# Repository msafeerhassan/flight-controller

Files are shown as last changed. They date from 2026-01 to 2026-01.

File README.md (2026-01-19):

# Custom Flight Controller
## A completely custom high-efficiency Flight Controller for Drone.
This flight controller is based on STM32F722RET6 MCU and BMI270 Gyro. This is optimized for modern FPV Drones featuring a 4 layer PCB and a dedicated 8-Pin connecter for modern ESC's.

### Hardware Specifications

MCU: STM32F722RET6

Gyro: BMI270 via Serial Peripheral Interface

Storage: W25NO1G

Input Voltage: 3S-6S LiPo (integrated 5V/2A Regulator)

OSD: AT7456E

Features: Buzzer for emergency situation, USB-C Programming, Suitable capacitors, diodes, inductors and resistors

### ESC Connection Guide
Pin 1 : VBAT : Battery Input

Pin 2 : GND : Ground

Pin 3 : Motor 1 : PB4

Pin 4 : Motor 2 : PB5

Pin 5 : Motor 3 : PB0

Pin 6 : Motor 4 : PB1

Pin 7 : Current : PC0

Pin 8 : Telemetry : PC7

### Software Specifications
Compatible with: 
- Betaflight
- Rotorflight
##### Code is given in firmware folder

### PCB:



### Schematic Diagram:



### Designed by Safeer Hassan :)

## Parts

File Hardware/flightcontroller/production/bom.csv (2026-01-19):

Designator | Footprint | Quantity | Value | LCSC Part #
BZ1 | Buzzer_12x9.5RM7.6 | 1 | Buzzer
C1, C12, C15, C16, C17, C18, C2, C3, C4, C6 | 0603 | 10 | 100nF
C10, C13, C8, R11, R12 | 0805 | 5 | 22uF
C11, C5, C9 | 0805 | 3 | 10uF
C14 | 0603 | 1 | 1uF
C19 | 0805 | 1 | 4.7uF
C7 | 0603 | 1 | 2.2uF
D1 | D_SOD-123 | 1 | B5819W_C8598
D2 | 0603 | 1 | GREEN LED
D3 | 0603 | 1 | RED LED
D4, D5 | D_SOD-123 | 2 | D_Schottky
D6 | D_DO-35_SOD27_P7.62mm_Horizontal | 1 | 1N4148
J1 | USB_C_Receptacle_HRO_TYPE-C-31-M-12 | 1 | USB_C_Receptacle_USB2.0
J3 | JST_GH_BM04B-GHS-TBT_1x04-1MP_P1.25mm_Vertical | 1 | A
J5 | Tag-Connect_TC2030-IDC-NL_2x03_P1.27mm_Vertical | 1 | JTAG_TC2030
L1 | L_6.3x6.3_H3 | 1 | CSME0418D-4R7M-LRH
P1 | JST_SHL_SM08B-SHLS-TF_1x08-1MP_P1.00mm_Horizontal | 1 | SM08B-SRSS-TB(LF)(SN) | C160407
Q1 | SOT-23 | 1 | MMBT2222A
R1, R2, R3, R4, R7, R8 | 0603 | 6 | 10k
R10, R9 | 1210 | 2 | 47uF
R13 | 0603 | 1 | 1k
R5, R6 | 0603 | 2 | 5.1k
SW1 | SW_Push_SPST_NO_Alps_SKRK | 1 | SW_Push
U2 | TSOT-23-6 | 1 | AP63205WU
U4 | SOT-23-6 | 1 | USBLC6-2SC6
U5 | SOT-23-5 | 1 | XC6220B331MR
U6 | LQFP-64_10x10mm_P0.5mm | 1 | STM32F722RETx
U7 | LGA-14_3x2.5mm_P0.5mm_LayoutBorder3x4y | 1 | BMI270
U8 | Bosch_LGA-8_2x2.5mm_P0.65mm_ClockwisePinNumbering | 1 | SPL06-001
U9 | WSON-8-1EP_8x6mm_P1.27mm_EP3.4x4.3mm | 1 | W25N01G
Y1 | Resonator_SMD_Murata_CSTxExxV-3Pin_3.0x1.1mm | 1 | 8MHz

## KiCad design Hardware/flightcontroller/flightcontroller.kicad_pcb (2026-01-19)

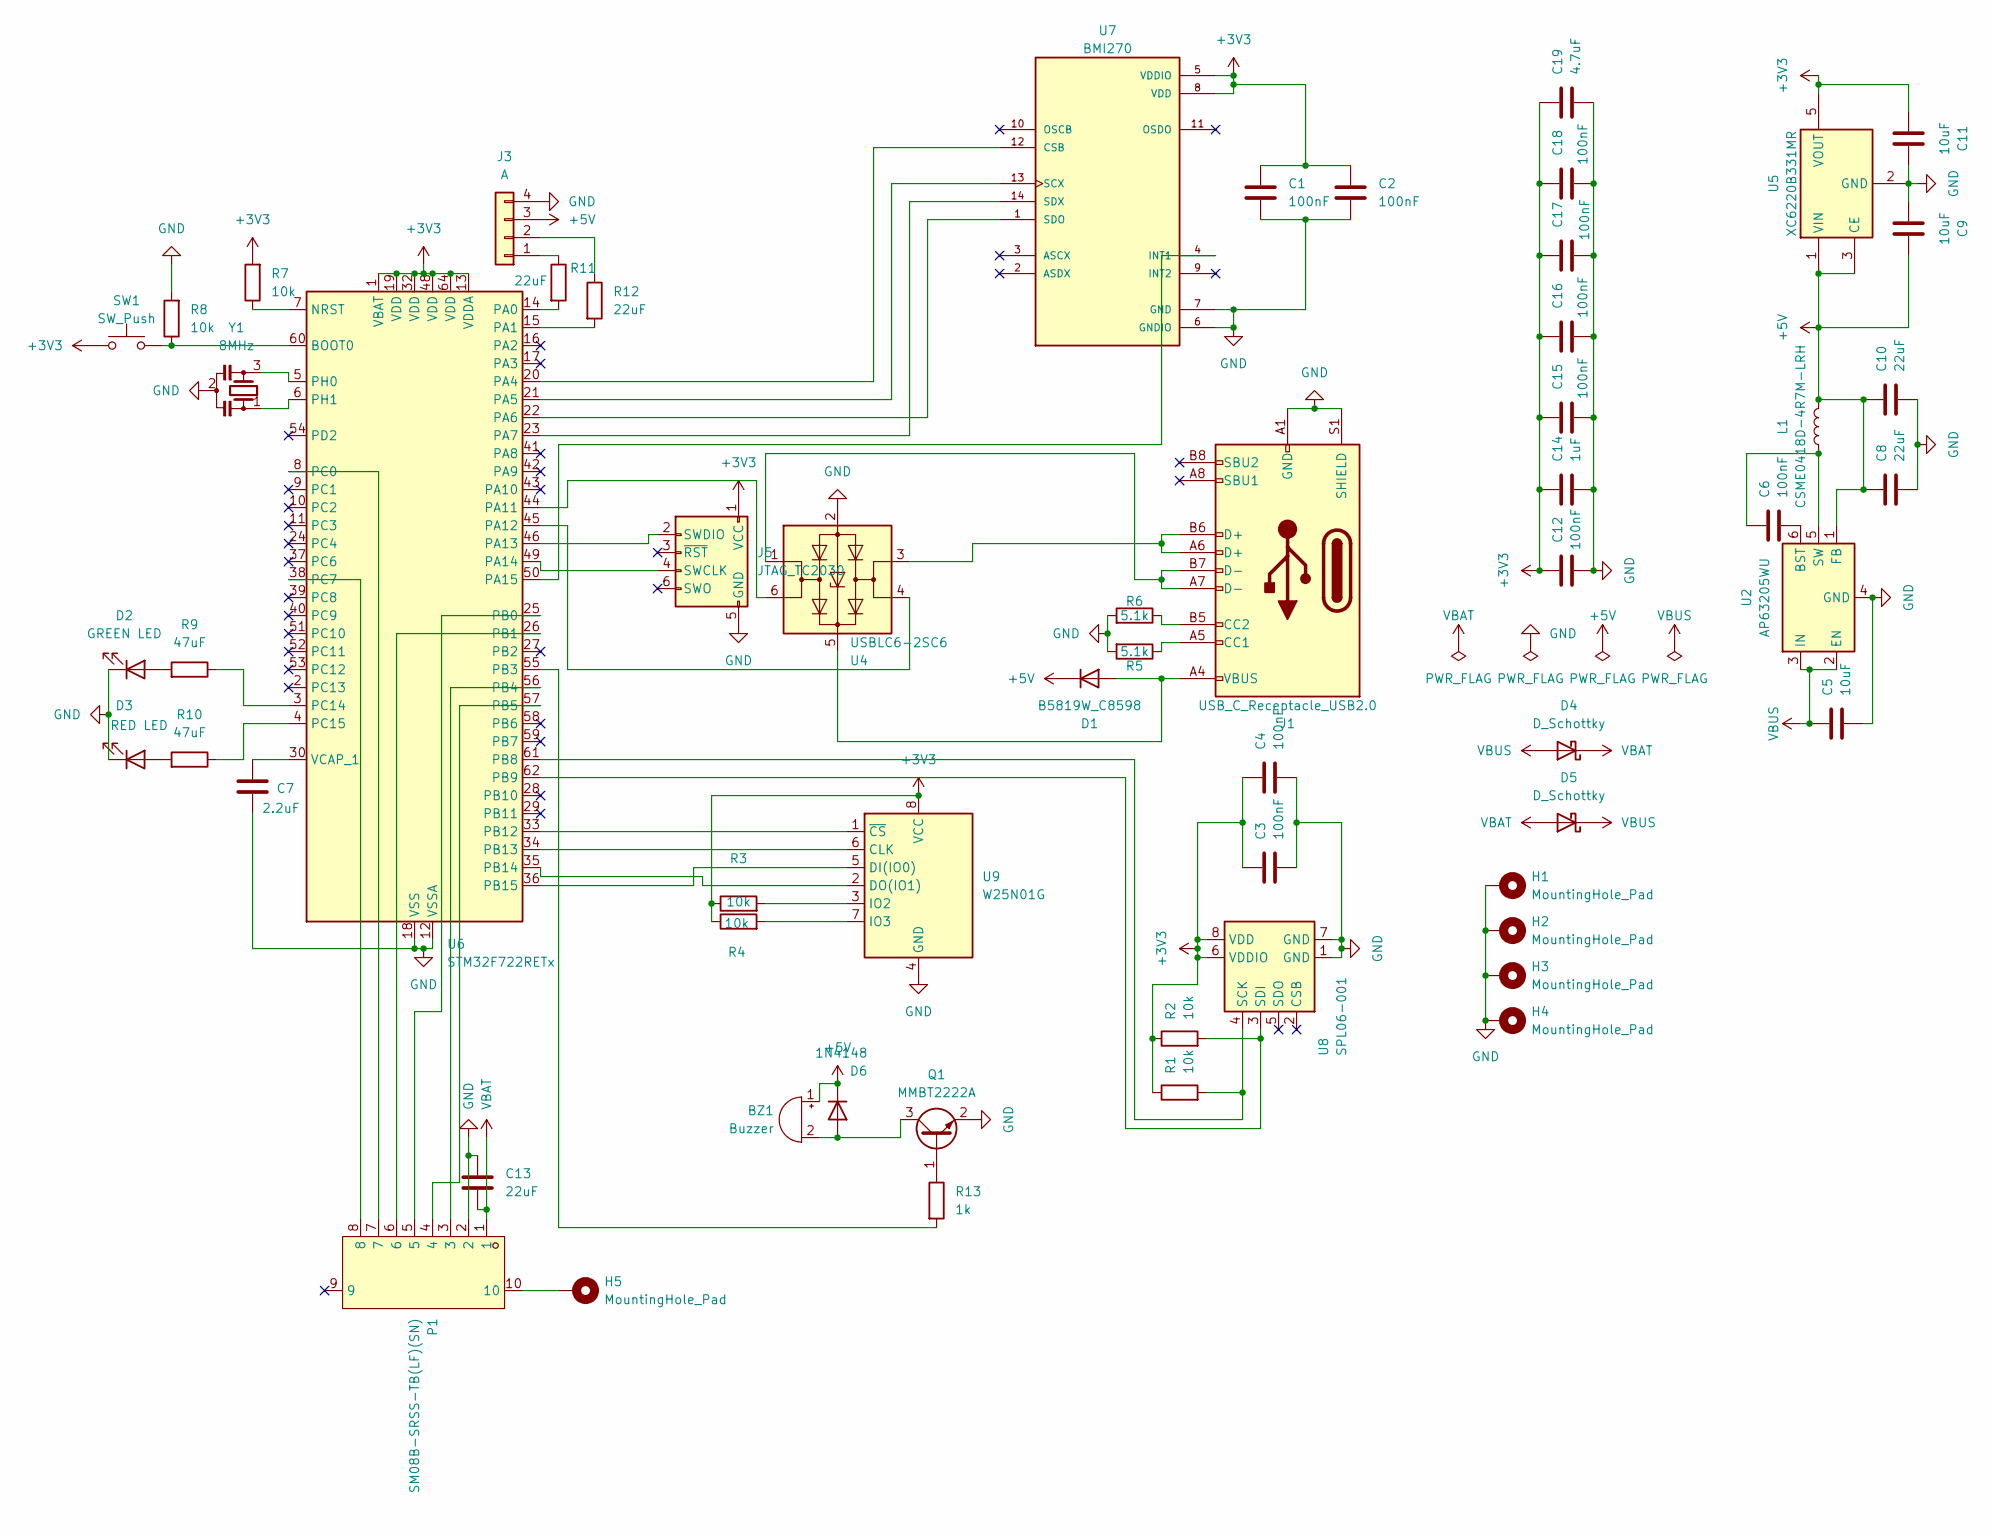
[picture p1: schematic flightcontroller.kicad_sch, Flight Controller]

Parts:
BZ1: Buzzer; Buzzer_12x9.5RM7.6
C1, C2, C3, C4, C6, C12, C15, C16, C17, C18: 100nF; C_0603_1608Metric
C5, C9, C11: 10uF; C_0805_2012Metric
C7: 2.2uF; C_0603_1608Metric
C8, C10, C13: 22uF; C_0805_2012Metric
C14: 1uF; C_0603_1608Metric
C19: 4.7uF; C_0805_2012Metric
D1: B5819W_C8598; D_SOD-123
D2: GREEN LED; LED_0603_1608Metric
D3: RED LED; LED_0603_1608Metric
D4, D5: D_Schottky; D_SOD-123
D6: 1N4148; D_DO-35_SOD27_P7.62mm_Horizontal
H1, H2, H3, H4, H5: MountingHole_Pad; MountingHole_3.2mm_M3_Pad_Via
J1: USB_C_Receptacle_USB2.0; USB_C_Receptacle_HRO_TYPE-C-31-M-12
J3: A; JST_GH_BM04B-GHS-TBT_1x04-1MP_P1.25mm_Vertical
J5: JTAG_TC2030; Tag-Connect_TC2030-IDC-NL_2x03_P1.27mm_Vertical
L1: CSME0418D-4R7M-LRH; L_6.3x6.3_H3
P1: SM08B-SRSS-TB(LF)(SN); JST_SHL_SM08B-SHLS-TF_1x08-1MP_P1.00mm_Horizontal; LCSC Part C160407
Q1: MMBT2222A; SOT-23
R1, R2, R3, R4, R7, R8: 10k; R_0603_1608Metric
R5, R6: 5.1k; R_0603_1608Metric
R9, R10: 47uF; C_1210_3225Metric
R11, R12: 22uF; C_0805_2012Metric
R13: 1k; R_0603_1608Metric
SW1: SW_Push; SW_Push_SPST_NO_Alps_SKRK
U2: AP63205WU; TSOT-23-6
U4: USBLC6-2SC6; SOT-23-6
U5: XC6220B331MR; SOT-23-5
U6: STM32F722RETx; LQFP-64_10x10mm_P0.5mm
U7: BMI270; LGA-14_3x2.5mm_P0.5mm_LayoutBorder3x4y
U8: SPL06-001; Bosch_LGA-8_2x2.5mm_P0.65mm_ClockwisePinNumbering
U9: W25N01G; WSON-8-1EP_8x6mm_P1.27mm_EP3.4x4.3mm
Y1: 8MHz; Resonator_SMD_Murata_CSTxExxV-3Pin_3.0x1.1mm

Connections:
+3V3: C1.1, C2.1, C3.1, C4.1, C11.1, C12.1, C14.1, C15.1, C16.1, C17.1, C18.1, C19.1, J5.1 (VCC), R1.1, R2.1, R3.1, R4.1, R7.2, SW1.1, U5.5 (VOUT), U6.1 (VBAT), U6.13 (VDDA), U6.19 (VDD), U6.32 (VDD), U6.48 (VDD), U6.64 (VDD), U7.5 (VDDIO), U7.8 (VDD), U8.6 (VDDIO), U8.8 (VDD), U9.8 (VCC)
+5V: BZ1.1 (+), C8.1, C9.2, C10.1, D1.1 (K), D6.1 (K), J3.3, L1.2, U2.1 (FB), U5.1 (VIN), U5.3 (CE)
GND: C1.2, C2.2, C3.2, C4.2, C5.2, C7.2, C8.2, C9.1, C10.2, C11.2, C12.2, C13.1, C14.2, C15.2, C16.2, C17.2, C18.2, C19.2, D2.1 (K), D3.1 (K), H1.1, H2.1, H3.1, H4.1, J1.A1 (GND), J1.A12 (GND), J1.B1 (GND), J1.B12 (GND), J1.S1 (SHIELD), J3.4, J5.5 (GND), P1.2, Q1.2 (E), R5.2, R6.2, R8.2, U2.4 (GND), U4.2 (GND), U5.2 (GND), U6.12 (VSSA), U6.18 (VSS), U6.31 (VSS), U6.47 (VSS), U6.63 (VSS), U7.6 (GNDIO), U7.7 (GND), U8.1 (GND), U8.7 (GND), U9.4 (GND), Y1.2
unnamed: BZ1.2 (-), D6.2 (A), Q1.3 (C)
unnamed: D1.2 (A), J1.A4 (VBUS), J1.A9 (VBUS), J1.B4 (VBUS), J1.B9 (VBUS), U4.5 (VBUS)
unnamed: D2.2 (A), R9.2
unnamed: D3.2 (A), R10.2
unnamed: H5.1, P1.10
unnamed: J1.A5 (CC1), R5.1
unnamed: J1.B5 (CC2), R6.1
unnamed: J1.A6 (D+), J1.B6 (D+), U4.3 (I/O2)
unnamed: J1.A7 (D-), J1.B7 (D-), U4.1 (I/O1)
unnamed: J3.1, R11.1
unnamed: J3.2, R12.1
unnamed: J5.4 (SWCLK), U6.49 (PA14)
unnamed: J5.2 (SWDIO), U6.46 (PA13)
unnamed: Q1.1 (B), R13.1
unnamed: C6.2, U2.6 (BST)
unnamed: C6.1, L1.1, U2.5 (SW)
unnamed: R8.1, SW1.2, U6.60 (BOOT0)
unnamed: R7.1, U6.7 (NRST)
unnamed: R11.2, U6.14 (PA0)
unnamed: R12.2, U6.15 (PA1)
unnamed: U6.20 (PA4), U7.12 (CSB)
unnamed: U6.21 (PA5), U7.13 (SCX)
unnamed: U6.22 (PA6), U7.1 (SDO)
unnamed: U6.23 (PA7), U7.14 (SDX)
unnamed: U4.6 (I/O1), U6.44 (PA11)
unnamed: U4.4 (I/O2), U6.45 (PA12)
unnamed: U6.50 (PA15), U7.4 (INT1)
unnamed: P1.5, U6.25 (PB0)
unnamed: P1.6, U6.26 (PB1)
unnamed: R13.2, U6.55 (PB3)
unnamed: P1.3, U6.56 (PB4)
unnamed: P1.4, U6.57 (PB5)
unnamed: R1.2, U6.61 (PB8), U8.4 (SCK)
unnamed: R2.2, U6.62 (PB9), U8.3 (SDI)
unnamed: U6.33 (PB12), U9.1 (~CS)
unnamed: U6.34 (PB13), U9.6 (CLK)
unnamed: U6.35 (PB14), U9.2 (DO(IO1))
unnamed: U6.36 (PB15), U9.5 (DI(IO0))
unnamed: P1.7, U6.8 (PC0)
unnamed: P1.8, U6.38 (PC7)
unnamed: R9.1, U6.3 (PC14)
unnamed: R10.1, U6.4 (PC15)
unnamed: U6.5 (PH0), Y1.3
unnamed: U6.6 (PH1), Y1.1
unnamed: C7.1, U6.30 (VCAP_1)
unnamed: R3.2, U9.3 (IO2)
unnamed: R4.2, U9.7 (IO3)
VBAT: C13.2, D4.1 (K), D5.2 (A), P1.1
VBUS: C5.1, D4.2 (A), D5.1 (K), U2.2 (EN), U2.3 (IN)

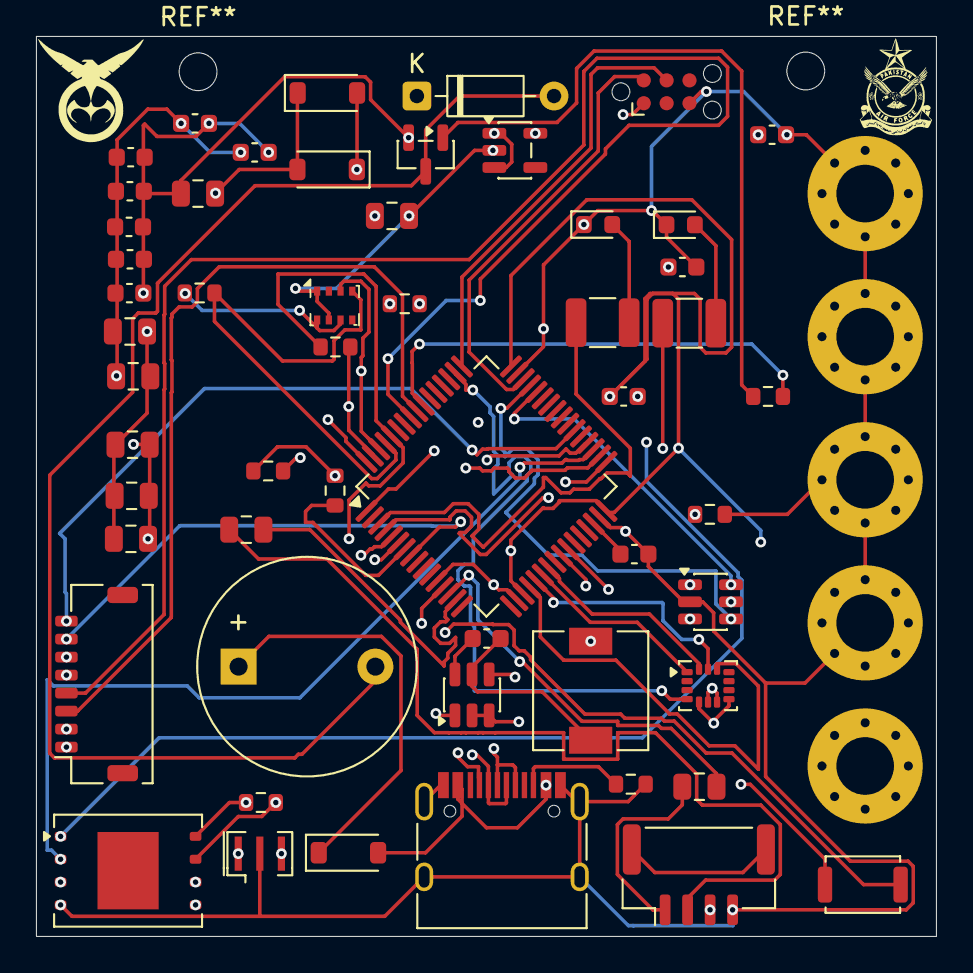
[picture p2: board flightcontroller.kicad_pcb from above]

Board: 4 copper layers, 50.0 x 50.0 mm, 59 parts (0 on the bottom side), 51 nets.

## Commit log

2026-01-19 full project commit
    [bom.csv, designators.csv, flightcontroller.kicad_pcb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]
2026-01-19 Enhance README with specifications and diagrams
    Added detailed hardware and software specifications, ESC connection guide, and schematic diagram to README.
2026-01-19 Update README with hardware specs and ESC guide
    Added hardware specifications and ESC connection guide to README.
